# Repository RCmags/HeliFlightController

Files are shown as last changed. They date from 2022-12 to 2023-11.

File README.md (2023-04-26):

# Flight controller for an RC helicopter :helicopter:

This arduino sketch is a flight controller for a 4ch radio-controlled helicopter. It uses an [MPU6050 IMU](https://invensense.tdk.com/products/motion-tracking/6-axis/mpu-6050/) to stabilize the aircraft. 

## How it works

The pitch, roll and yaw axes are stabilized with a respective [PID controller](https://en.wikipedia.org/wiki/PID_controller) using the angular velocity as a proportional term. The yaw axis includes a counter-torque term that increases with throttle. 

In general, the program only improves stability in the _short-term_ and a pilot (or other control algorithm) is needed to stabilize the helicopter in the _long-term_. Despite this, the aircraft can maintain a steady hover without pilot input if the PIDs are tuned correctly (in the order of 5 seconds).  

## Receiver Inputs

The program is designed to receive __4 PWM inputs__ from an RC receiver and generates __3 PWM outputs__. Two signals go to the cyclic servos and the third goes to the tail-servo or speed controller. Since it assumes that only two servos are used for the cyclic, only a [90-degree swashplate](https://www.rchelicopterfun.com/ccpm.html) is supported. The code assumes the transmitter uses MODE 2, but MODE 1 can be used by swapping the arduino connections to the receiver.

## Schematic
The sketch was written for an Arduino Nano but it should be compatible with other boards.

<p align="center">
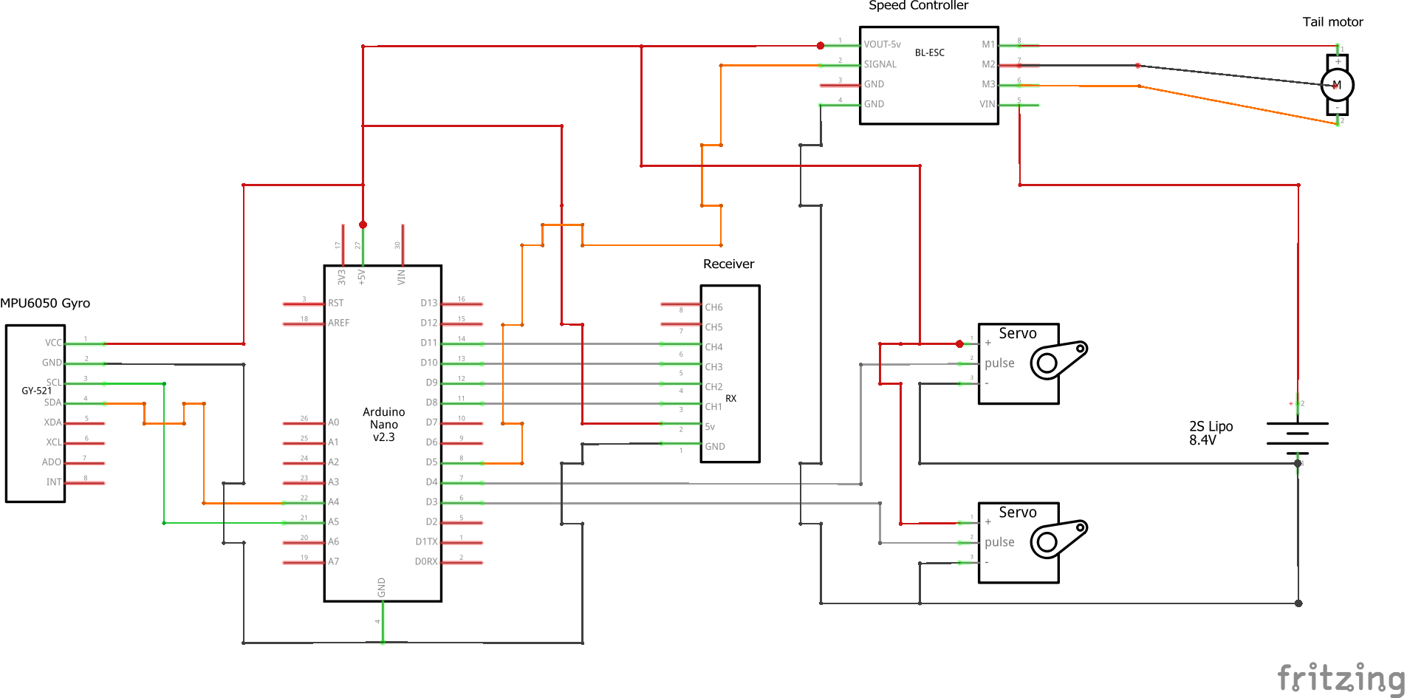
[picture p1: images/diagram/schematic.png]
 
</p>

__Note__: replace the tail motor and speed controller with a servo if you're using a variable pitch rotor.

## Dependencies
These libraries are needed to compile the code:

- [basicMPU6050](https://github.com/RCmags/basicMPU6050)
- [imuFilter](https://github.com/RCmags/imuFilter)

## Example
This is the helicopter the code was initially writen for:

See: [Flight video](https://www.youtube.com/watch?v=nHYoC72DZKo)

<p align="center">
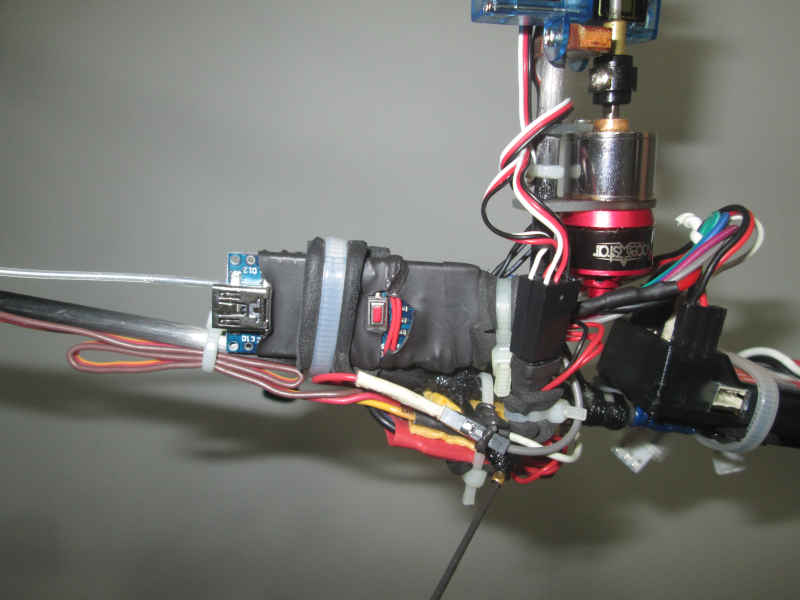
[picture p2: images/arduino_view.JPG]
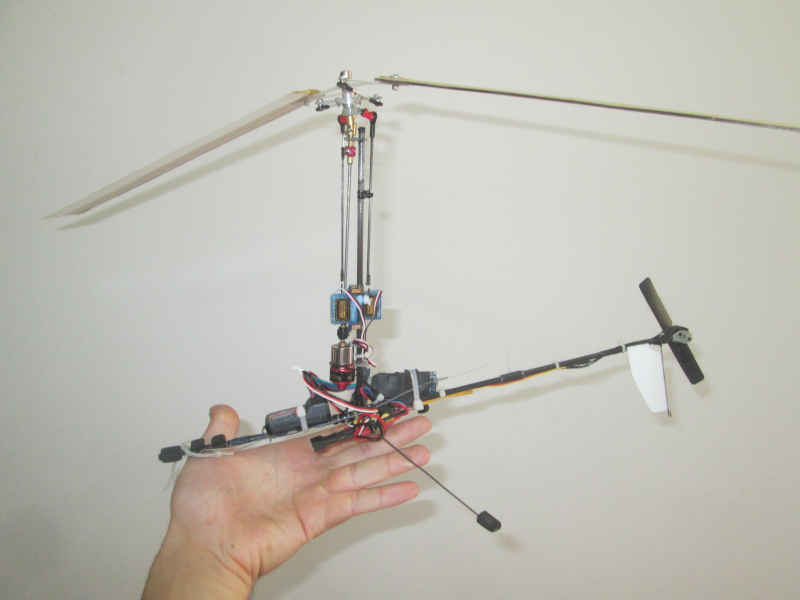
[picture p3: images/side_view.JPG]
  
</p>

<p align="center">
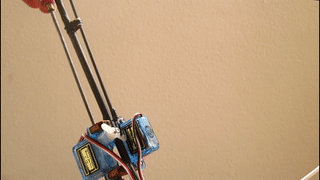
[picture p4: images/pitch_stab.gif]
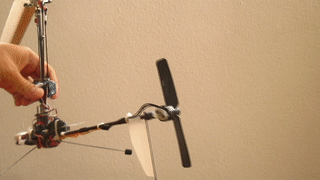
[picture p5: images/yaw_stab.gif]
 
</p>

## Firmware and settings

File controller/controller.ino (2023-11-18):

/* HELICOPER FLIGHT CONTROLLER */

/* Arduino NANO sketch to stabilize a 4ch RC helicopter controlled by cyclic or weight shift. 
 * It commands two cyclic servos and a tail servo/ESC to stabilize each axis.
 * Author: RCmags https://github.com/RCmags
 * 
 * NOTE: 
 * This sketch uses an MPU6050 IMU (gyroscope and accelerometer) to stabilize the vehicle. It assumes 
 * that only lift and gravity act on the aircraft, and that any external torques are negligible.
*/
//=============== Connections ================
// See included schematic
  // Inputs:
// Pin 8  -> Receiver CH1
// Pin 9  -> Receiver CH2
// Pin 10 -> Receiver CH4
// Pin 11 -> Receiver CH3
  // Outputs:
// Pin 3  -> Pitch servo
// Pin 4  -> Roll servo 
// Pin 5  -> Tail servo / ESC  
// Pin A0 -> Tail servo / ESC  

//=================== Code ===================

#include "parameters.h"
#include "receiver.h"
#include "imu.h"
#include "fusion.h"
#include "pid.h"
#include "servos.h"

//----- Main loop

void setup() { 
  digitalWrite(LED_BUILTIN, LOW); 
  delay(1000);       // Allow RX to startup
  
  setupISR();
  setupServos();
  
  imu.setup();
  imu.setBias();

  #ifdef USING_AUTO_LEVEL
    setupFusion();
  #endif

  digitalWrite(LED_BUILTIN, HIGH);
}

void loop() {
  // RX inputs
  float input[4]; filterInputs(input);            // get RX inputs

  // controller output
  imu.updateBias();
  
  float output[4]; PIDcontroller(input, output);

  #ifdef USING_TAIL_ROTOR
    output[2] += torqueBias( input[3] );          // anti-torque
  #endif

  // move servos
  servoPosition(output);   
}

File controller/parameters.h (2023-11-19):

/*      CONSTANT     |    VALUE   |  UNIT  |   DESCRIPTION */
/*=========================================================*/
//                  1. Control inputs
//----------------------------------------------------------
#define GAIN_PITCH       0.8                 // Pitch servo
#define GAIN_ROLL        0.8                 // Roll servo
#define GAIN_YAW         1.6                 // Yaw servo / Tail ESC

//----------------------------------------------------------
//                  2A. Heading stabilization
//---------------------------s-------------------------------
/* NOTE: For a given axis, the propotional, integral and 
         derivative terms must have the same sign */
  // I. Proportional:                         // Proportional gain. Adjusts damping response. Increase to retard rotation. 
#define GAIN_PROP_ROLL    110.0
#define GAIN_PROP_PITCH   280.0
#define GAIN_PROP_YAW     18.0
  
  // II. Integral:                            // Integral gain. Adjusts spring respose. Increase to have a stronger restoring force.
#define GAIN_INT_ROLL     700.0 //700
#define GAIN_INT_PITCH    700.0 //900
#define GAIN_INT_YAW      150.0

  // III. Derivative:                         // Derivative gain. Reduces oscillations of proportional term. Magnifies vibration noise.
#define GAIN_DERIV_ROLL   4.0
#define GAIN_DERIV_PITCH  7.0
#define GAIN_DERIV_YAW    1.0

  // IV. Phase angle
#define STAT_ANGLE        60.0     // deg      // Pitch-roll coupling angle. Adjust until control axes respond independently.
#define DYN_ANGLE         60.0     // deg

  // V. Other:      
#define NEGATE_ROLL                            // Uncomment to reverse roll deflection
//#define NEGATE_PITCH                           // Uncomment to reverse pitch deflection
//#define NEGATE_YAW                             // Uncomment to reverse yaw deflection

/* NOTE: must enable integral decay to use */
#define DECAY_ROTOR       0                   // Decay rate of pitch/roll integral term. 
#define DECAY_YAW         0                   // Decay rate of yaw integral term. Increase to have integral term reduce with time. 

//----------------------------------------------------------
//                  2B. Auto level
//----------------------------------------------------------
/* NOTE: must enable auto level to use */
#define TRIM_ANG_PITCH    -5.0                // trim to self-level aircraft in pitch
#define TRIM_ANG_ROLL    -10.0                // trim to self-level aircraft in roll

//----------------------------------------------------------
//                  3. Servo trims
//----------------------------------------------------------
#define TRIM_PITCH        0       // us       // Pitch servp
#define TRIM_ROLL         0       // us       // Roll servo
#define TRIM_YAW          0       // us       // Yaw servo / Tail ESC

//----------------------------------------------------------
//                  4. Signal filters
//----------------------------------------------------------
#define NUMBER_MEAN       50                  // number of readings used for input calibration
#define INPUT_DEADBAND    24      // us       // deadband near center-stick to prevent integrator drift.
#define INPUT_CHANGE      4       // us       // Change in PWM signal needed to update receiver inputs
#define ALPHA             0.4                /* Gain of alpha-beta filter applied to sensor input. 
                                               A smaller value smoothens the derivative at the cost of slower response */
//----------------------------------------------------------
//                  5. Tail rotor counter-torque
//---------------------------------------------------------- 
#define TORQUE_POWER      0.5                 /* Exponent of tail rotor correction curve. Make smaller to have 
                                                 correction change faster at low throttle. */
#define TORQUE_GAIN       250                 // Magnitude of tail rotor correction. Increase to apply a larger counter-torque. 

//----------------------------------------------------------
//                  6. Output PWM signal
//----------------------------------------------------------
#define PWM_MID           1500    // us       // Center/middle servo position
#define PWM_CHANGE        550     // us       // Maximum change in servo position

//----------------------------------------------------------
//                  7. Settings
//---------------------------------------------------------- 
//#define USING_WEIGHT_SHIFT                    // Uncomment for weight-shift control 
//#define USING_TAIL_ROTOR                      // Uncomment for tail rotor correction
//#define USING_INTEGRAL_DECAY                  // Uncomment to enable integral decay
#define USING_AUTO_LEVEL                      // Uncomment to enable self-leveling correction

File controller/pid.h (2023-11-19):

//============= PID controller =============

/* Linearized error function */
vec3_t crossAngle(vec3_t v1, vec3_t v2) {
  vec3_t cross = v1.cross(v2);  // sin
  float  dot   = v1.dot(v2);    // cos
  
  // triangle wave approximation
  float scale = 0.5 + (1.1 - 0.1*dot*dot)/(1 + 0.9*dot);
  return cross*scale;
}

/* Apply PID controller to each rotational axis */
void PIDcontroller( float* input, float* output ) {
  // 1. Time step:
  static uint32_t time_last = micros()-1;  // dither initial measurement (avoid zero division)
   
  uint32_t time_now = micros();
  float dt = float(time_now - time_last)*1e-6;
  time_last = time_now;

  // 0. Constants:
      // PID coefficients:
  constexpr float DECAY[]      = { DECAY_ROTOR    , DECAY_ROTOR     , DECAY_YAW      };
  constexpr float GAIN_PROP[]  = { GAIN_PROP_ROLL , GAIN_PROP_PITCH , GAIN_PROP_YAW  };
  constexpr float GAIN_INT[]   = { GAIN_INT_ROLL  , GAIN_INT_PITCH  , GAIN_INT_YAW   };
  constexpr float GAIN_DERIV[] = { GAIN_DERIV_ROLL, GAIN_DERIV_PITCH, GAIN_DERIV_YAW };
    
    // integral term:
  constexpr float SCALE = (DEG_TO_RAD * 150) / 500.0;   // control input rate. Convert 500us to 150 deg/s 
    
    // alpha-beta filter:
  constexpr float BETA = ALPHA * ALPHA * 0.25;

  // 1. Calculus
  static float angle[3] = {0};      // integral
  static float angacc[3] = {0};     // derivative
  static float angvel_s[3] = {0};   // smoothed proportional

  float angvel[] = { gyroX(), gyroY(), gyroZ() };
  float angvel_t[] = { input[0]*SCALE, 
                       input[1]*SCALE,
                       input[2]*SCALE };
                       
  #ifdef USING_AUTO_LEVEL    
    // offsets
    constexpr float ANG_ROLL = TRIM_ANG_ROLL * DEG_TO_RAD;
    constexpr float ANG_PITCH = TRIM_ANG_PITCH * DEG_TO_RAD;

    // yaw change
    float dyaw = -0.5 * angvel_t[2] * dt;
    fusion.rotateHeading( dyaw, SMALL_ANGLE );

    // heading error
    updateFusion();

      // target
    vec3_t vec_rot = vec3_t( angvel_t[0], angvel_t[1], 0 ) * 0.25;
    
    quat_t quat_rot; 
    quat_rot.setRotation( vec_rot, SMALL_ANGLE );
    quat_rot = quat_rot.norm();

    vec3_t vec_z = quat_rot.rotate( vec3_t(0,0,1) , LOCAL_FRAME );
    vec3_t vec_y = quat_rot.rotate( vec3_t(0,1,0) , LOCAL_FRAME );
    vec3_t vec_x = quat_rot.rotate( vec3_t(1,0,0) , LOCAL_FRAME );

      // measure
    vec3_t error; 
    error  = crossAngle( fusion.getZaxis(LOCAL_FRAME), vec_z );
    error += crossAngle( fusion.getYaxis(LOCAL_FRAME), vec_y );
    error += crossAngle( fusion.getXaxis(LOCAL_FRAME), vec_x );
    error *= 0.5;
    
      // covert to channel axes
    angle[0] = GAIN_INT[0] * error.x;    // roll
    angle[1] = GAIN_INT[1] * error.y;    // pitch
    angle[2] = GAIN_INT[2] * error.z;    // yaw
  #endif
  
  for( int i = 0; i < 3; i += 1 ) {
    // alpha-beta filter:
    float dvel = angvel[i] - angvel_s[i];
    angvel_s[i] += angacc[i]*dt + ALPHA*dvel;   // smoothed proportional
    angacc[i] += BETA*dvel / dt;                // derivative

    // target rate
    float dangvel = angvel[i] - angvel_t[i]; 
    
    // integrate
    angvel[i] += angacc[i] * 0.5 * dt;           // trapezoidal rule. Use derivative to improve area slice. 

    #ifndef USING_AUTO_LEVEL
      angle[i] += GAIN_INT[i] * dangvel * dt;    // Use quaternion? Need to prevent saturation.
      
      #ifdef USING_INTEGRAL_DECAY
        angle[i] -= DECAY[i] * angle[i] * dt;       
      #endif
   #endif
    
    angle[i] = constrain(angle[i], -PWM_CHANGE, PWM_CHANGE);  // prevent windup
  }

  // yaw axis
  output[2] = GAIN_PROP[2]*(angvel[2] - angvel_t[2]) + angle[2] + GAIN_DERIV[2]*angacc[2];

  // 3. Phase angle mixing

    // dynamic angle
  constexpr float DYN_ANG = DYN_ANGLE * DEG_TO_RAD;
  constexpr float SIN_DYN = sin(DYN_ANG);
  constexpr float COS_DYN = cos(DYN_ANG);
  
  float dyn_x = GAIN_PROP[0]*angvel[0] + GAIN_DERIV[0]*angacc[0];
  float dyn_y = GAIN_PROP[1]*angvel[1] + GAIN_DERIV[1]*angacc[1];

  output[0] = dyn_x*COS_DYN + dyn_y*SIN_DYN;
  output[1] = dyn_y*COS_DYN - dyn_x*SIN_DYN; 

    // static angle
  constexpr float ANGLE = DEG_TO_RAD * STAT_ANGLE;
  constexpr float SIN_ANG = sin(ANGLE);
  constexpr float COS_ANG = cos(ANGLE);

  float stat_x = -GAIN_PROP[0]*angvel_t[0] + angle[0];
  float stat_y = -GAIN_PROP[1]*angvel_t[1] + angle[1];
  
  float output_0 = output[0];
  output[0] += stat_x*COS_ANG + stat_y*SIN_ANG;
  output[1] += stat_y*COS_ANG - stat_x*SIN_ANG;
  
  // 3. parameters:
  
  #ifdef USING_WEIGHT_SHIFT
    float accel = accelZ();
    float gain = accel == 0 ? 0 : 1/accel;    // deflection must increase with lower lift
    output[0] *= gain;
    output[1] *= gain;
  #endif

  #ifdef NEGATE_ROLL
    output[0] = -output[0];
  #endif

  #ifdef NEGATE_PITCH
    output[1] = -output[1];
  #endif

  #ifdef NEGATE_YAW
    output[2] = -output[2];
  #endif
}

// counter main-rotor torque via yaw bias
float torqueBias(float input) {
  constexpr float SCALE = 0.5 / PWM_CHANGE;
  input = input < 0 ? 0 : input;
  input *= SCALE;
  return pow(input, TORQUE_POWER) * TORQUE_GAIN;  
}

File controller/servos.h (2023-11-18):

//=========== Servos / Tail ESC ============
#include <Servo.h>
Servo servo[3];

//---------------------- Constants -------------------------

constexpr float PWM_MID_SERVO[] = { PWM_MID + TRIM_PITCH, 
                                    PWM_MID + TRIM_ROLL, 
                                    PWM_MID + TRIM_YAW };
                                    
constexpr int SERVO_PIN[] = {3,4,5};    // Output pins: roll, pitch, yaw

//---------------------------------------------------------

/* initialize and center servos */
void setupServos() {  
  for( int i=0; i < 3; i += 1 ) {
    pinMode( SERVO_PIN[i], OUTPUT);
    servo[i].attach( SERVO_PIN[i] );
    servo[i].writeMicroseconds( PWM_MID_SERVO[i] );  
  }
}

/* set servo positions */
void servoPosition( float* output ) {
  for( int i=0; i < 3; i += 1 ) {
    output[i] = constrain( output[i], -PWM_CHANGE, PWM_CHANGE);
    servo[i].writeMicroseconds( PWM_MID_SERVO[i] + output[i] );  
  }
}

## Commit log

2023-01-01 accelerometer sign
2023-04-24 fixed schematic image
2023-04-24 add fritzing diagram
    [HeliFlightControl.fzz]
2023-11-18 imu angle as integral
2023-11-19 quaternion upright
    [HeliFlightControl.fzz]
